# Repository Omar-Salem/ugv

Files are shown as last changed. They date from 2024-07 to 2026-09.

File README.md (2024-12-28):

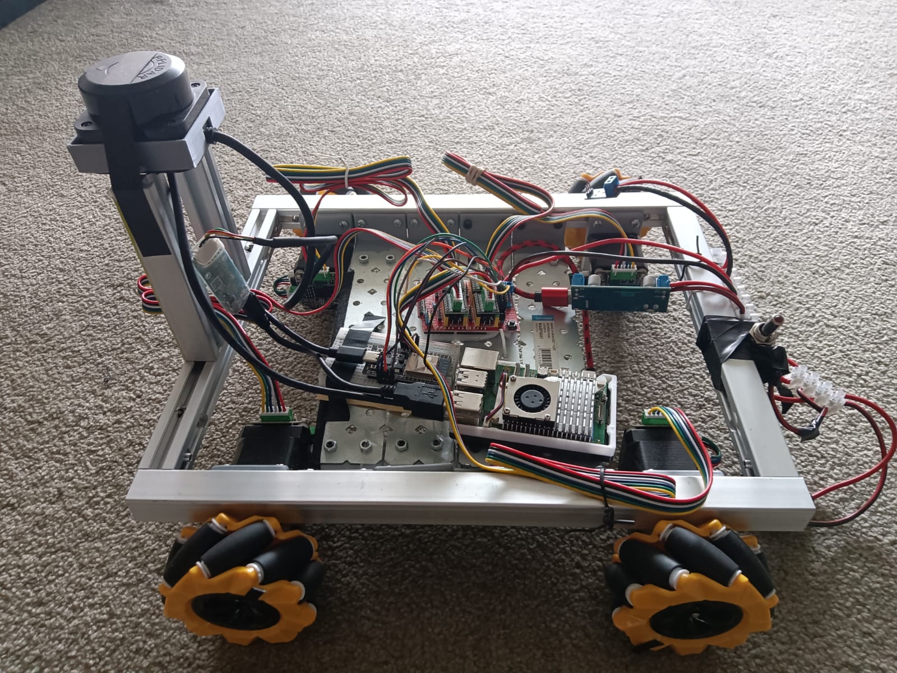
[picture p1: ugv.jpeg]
UGV


# Requirements
## Jazzy
```bash
sudo apt update && sudo apt upgrade

# Set locale
locale  # check for UTF-8

sudo apt install locales
sudo locale-gen en_US en_US.UTF-8
sudo update-locale LC_ALL=en_US.UTF-8 LANG=en_US.UTF-8
export LANG=en_US.UTF-8

locale  # verify settings

# You will need to add the ROS 2 apt repository to your system.
sudo apt install software-properties-common -y
sudo add-apt-repository universe -y

# Now add the ROS 2 GPG key with apt.
sudo apt update && sudo apt install curl -y
sudo curl -sSL https://raw.githubusercontent.com/ros/rosdistro/master/ros.key -o /usr/share/keyrings/ros-archive-keyring.gpg

# Then add the repository to your sources list.
echo "deb [arch=$(dpkg --print-architecture) signed-by=/usr/share/keyrings/ros-archive-keyring.gpg] http://packages.ros.org/ros2/ubuntu $(. /etc/os-release && echo $UBUNTU_CODENAME) main" | sudo tee /etc/apt/sources.list.d/ros2.list > /dev/null

# Install development tools 
sudo apt update && sudo apt install ros-dev-tools

# Install ROS 2
sudo apt update && sudo apt upgrade && sudo apt install ros-jazzy-desktop -y

sudo tee -a ~/.bashrc <<EOL
export ROS_DOMAIN_ID=0
export QT_QPA_PLATFORM=xcb rviz2
export RMW_IMPLEMENTATION=rmw_cyclonedds_cpp
source /opt/ros/jazzy/setup.bash
source ~/microros_ws/install/local_setup.bash
EOL
source ~/.bashrc
sudo apt-get install python3-rosdep -y
echo ${ROS_DISTRO}
````
## Packages
````bash
sudo apt-get install -y ros-${ROS_DISTRO}-slam-toolbox ros-${ROS_DISTRO}-joint-state-publisher ros-${ROS_DISTRO}-robot-state-publisher ros-${ROS_DISTRO}-xacro
sudo apt install -y ros-${ROS_DISTRO}-ros2-control
sudo apt install -y ros-${ROS_DISTRO}-joint-state-publisher-gui
sudo apt install -y ros-${ROS_DISTRO}-ros2-controllers
sudo apt install -y ros-${ROS_DISTRO}-robot-localization
sudo apt install -y ros-${ROS_DISTRO}-navigation2
sudo apt install -y ros-${ROS_DISTRO}-nav2-bringup
sudo apt install -y ros-${ROS_DISTRO}-controller-manager
sudo apt install -y ros-${ROS_DISTRO}-rosbag2
sudo apt install -y ros-${ROS_DISTRO}-behaviortree-cpp-v3
sudo apt install -y ros-${ROS_DISTRO}-tf-transformations
sudo apt-get install -y ros-${ROS_DISTRO}-image-tools
sudo apt-get install -y ros-${ROS_DISTRO}-cartographer

sudo apt install -y ros-${ROS_DISTRO}-angles
sudo apt install -y ros-${ROS_DISTRO}-mqtt-client
sudo apt install -y ros-${ROS_DISTRO}-launch-xml
sudo apt install -y ros-${ROS_DISTRO}-rmw-cyclonedds-cpp ros-${ROS_DISTRO}-tf2-ros ros-${ROS_DISTRO}-tf2-tools
sudo apt install -y python3-colcon-common-extensions
sudo apt-get install -y ros-${ROS_DISTRO}-rviz2 
sudo apt install -y ros-${ROS_DISTRO}-ros-gz
sudo apt install -y ros-${ROS_DISTRO}-gz-ros2-control
sudo apt install vim -y
sudo usermod -aG dialout ${USER}
````

## microros
https://www.hackster.io/514301/micro-ros-on-esp32-using-arduino-ide-1360ca
````bash
cd ~
mkdir microros_ws
cd microros_ws
git clone -b $ROS_DISTRO https://github.com/micro-ROS/micro_ros_setup.git src/micro_ros_setup
sudo apt update && rosdep update
rosdep install --from-paths src --ignore-src -y
sudo apt-get install -y python3-pip
colcon build
source install/local_setup.bash
ros2 run micro_ros_setup create_agent_ws.sh
ros2 run micro_ros_setup build_agent.sh
````

## ROS Control Determinism
````bash
sudo addgroup realtime && sudo usermod -a -G realtime $(whoami)

sudo tee -a /etc/security/limits.conf <<EOL
@realtime soft rtprio 99
@realtime soft priority 99
@realtime soft memlock 102400
@realtime hard rtprio 99
@realtime hard priority 99
@realtime hard memlock 102400
EOL
````

## Git config and SSH key
````bash
git config --global user.email "omar.gamil.salem@gmail.com"
git config --global user.name "Omar Salem"
ssh-keygen -t ed25519 -C "omar.gamil.salem@gmail.com"
cat ~/.ssh/id_ed25519.pub
````

## Create workspace and clone repo
````bash
mkdir -p ~/ugv_ws/src
cd ~/ugv_ws/src 
git clone git@github.com:Omar-Salem/ugv.git .
cd ~/ugv_ws
colcon build 
````

## Shutdown shortcut
````bash
echo "alias off='sudo shutdown -h now'" >> ~/.bash_aliases
````

## Run
### Display

```bash
cd ~/ugv_ws && colcon build --packages-select ugv_description && source install/setup.bash && ros2 launch ugv_description display.launch.py use_gui:=true use_joint_state_publisher:=true
```

### Control
```bash
cd ~/ugv_ws && colcon build --packages-select ugv_control && source install/setup.bash && ros2 launch ugv_control gazebo.launch.py
```

### Mapping
```bash
cd ~/ugv_ws && colcon build --packages-select ugv_mapping && source install/setup.bash && ros2 launch ugv_mapping gazebo.launch.py
```

### Navigation
```bash
cd ~/ugv_ws && colcon build --packages-select ugv_nav && source install/setup.bash && ros2 launch ugv_nav gazebo.launch.py
```

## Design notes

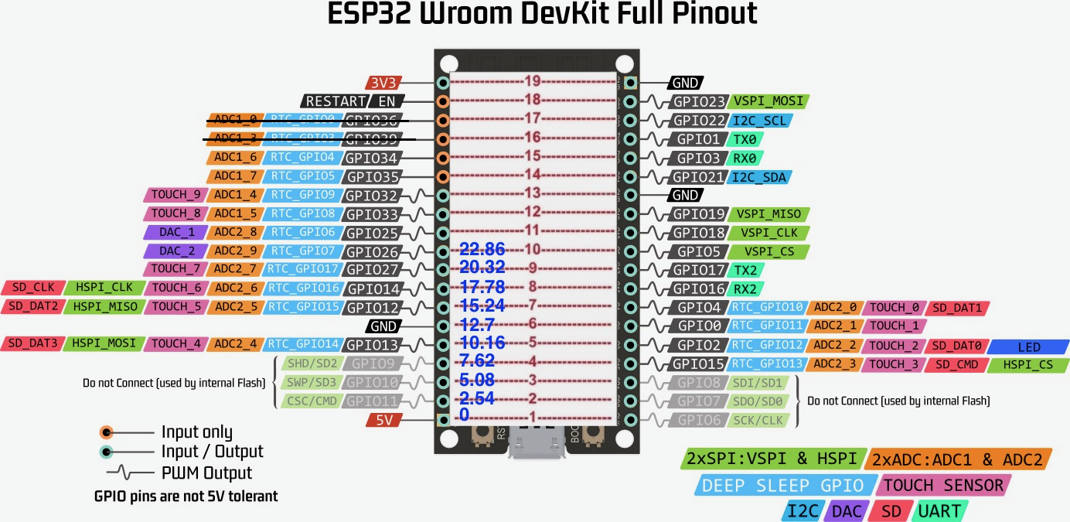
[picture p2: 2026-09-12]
ugv_firmware/docs/esp32 breadboard pinout.png

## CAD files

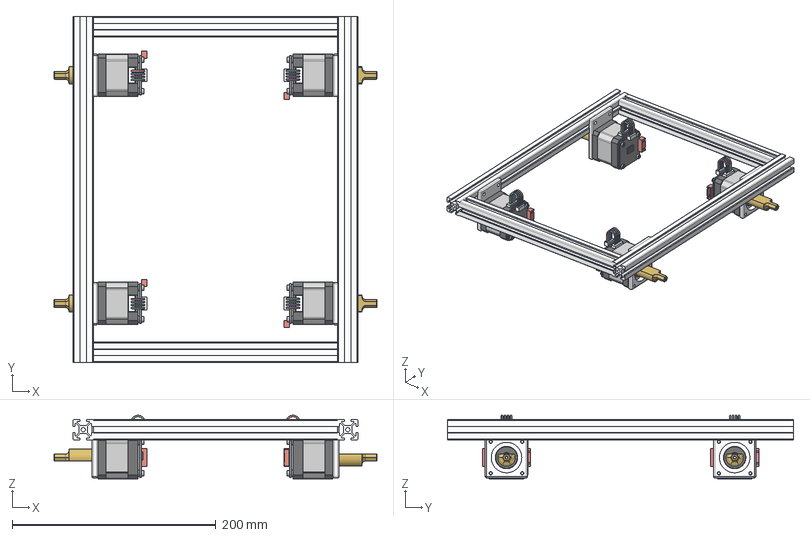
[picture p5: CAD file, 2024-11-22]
base_link_colour.step
317.3 x 340.0 x 62.6 mm
base_link
Motor
Motor (1)
Motor (2)
Motor (2) (1)

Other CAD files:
base_link_colour.f3d
ugv.f3d

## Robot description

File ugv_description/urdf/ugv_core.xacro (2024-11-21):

<?xml version="1.0"?>
<robot name="ugv" xmlns:xacro="http://www.ros.org/wiki/xacro">

    <xacro:include filename="$(find ugv_description)/gazebo/common_inertias.xacro" />

    <xacro:property name="wheel_radius" value="0.0395" />
    <xacro:property name="wheel_thickness" value="0.0369" />
    <xacro:property name="wheel_mass" value="0.05" />

    <xacro:property name="chassis_length" value="0.34" />
    <xacro:property name="chassis_width" value="0.285" />
    <xacro:property name="chassis_height" value="0.02" />
    <xacro:property name="chassis_mass" value="1.0" />
    <xacro:property name="chassis_offset_z" value="${wheel_radius}" />

    <xacro:property name="lidar_radius" value="0.02" />
    <xacro:property name="lidar_thickness" value="0.1" />
    <xacro:property name="lidar_mass" value="0.05" />

    <xacro:property name="edge_thickness" value="0.02" />
    <xacro:property name="edge_to_motor_mount" value="0.016" />
    <xacro:property name="motor_mount_width" value="0.0417" />
    <xacro:property name="motor_shaft_to_edge_x" value="${edge_thickness+edge_to_motor_mount+motor_mount_width/2}" />
    <xacro:property name="wheel_offset_x" value="${chassis_length/2-motor_shaft_to_edge_x}" />

    <xacro:property name="wheels_y_distance_edge_to_edge" value=".36"/>
    <xacro:property name="wheel_offset_y" value="${wheels_y_distance_edge_to_edge/2 - wheel_thickness/2}"/>

    <xacro:property name="wheel_offset_z" value="0.01" />

    <material name="orange">
        <color rgba="1 0.3 0.1 1" />
    </material>

    <material name="yellow">
        <color rgba="1 1 0 1" />
    </material>

    <material name="black">
        <color rgba="0 0 0 1" />
    </material>

    <xacro:macro name="wheel" params="prefix">
        <link name="${prefix}_wheel">
            <visual>
                <origin rpy="${pi/2} 0 0" xyz="0 0 0"/>
                <geometry>
                    <cylinder radius="${wheel_radius}" length="${wheel_thickness}" />
                </geometry>
                <material name="orange" />
            </visual>
            <collision>
                <origin rpy="${pi/2} 0 0" xyz="0 0 0"/>
                <geometry>
                    <cylinder radius="${wheel_radius}" length="${wheel_thickness}" />
                </geometry>
            </collision>
            <xacro:inertial_cylinder mass="${wheel_mass}" length="${wheel_thickness}" radius="${wheel_radius}">
                <origin xyz="0 0 0" rpy="0 0 0" />
            </xacro:inertial_cylinder>
        </link>
    </xacro:macro>

    <link name="base_link">
        <visual>
            <origin rpy="0 0 0" xyz="0 0 ${chassis_offset_z}"/>
            <geometry>
                <box size="${chassis_length} ${chassis_width} ${chassis_height}" />
            </geometry>
            <material name="black" />
        </visual>
        <collision>
            <origin rpy="0 0 0" xyz="0 0 ${chassis_offset_z}"/>
            <geometry>
                <box size="${chassis_length} ${chassis_width} ${chassis_height}" />
            </geometry>
        </collision>
        <xacro:inertial_box mass="${chassis_mass}" x="${chassis_length}" y="${chassis_width}" z="${chassis_height}">
            <origin rpy="0 0 0" xyz="0 0 ${chassis_offset_z}"/>
        </xacro:inertial_box>
    </link>

    <link name="base_footprint" />

    <joint name="base_footprint_joint" type="fixed">
        <parent link="base_link" />
        <child link="base_footprint" />
        <origin xyz="0 0 0" rpy="0 0 0" />
    </joint>

    <xacro:wheel prefix="front_right" />


    <joint name="front_right_wheel_joint" type="continuous">
        <parent link="base_link" />
        <child link="front_right_wheel" />
        <origin xyz="${wheel_offset_x} ${-wheel_offset_y} ${wheel_radius}" />
        <axis xyz="0.0 1.0 0.0" />
    </joint>


    <xacro:wheel prefix="front_left" />

    <joint name="front_left_wheel_joint" type="continuous">
        <parent link="base_link" />
        <child link="front_left_wheel" />
        <origin xyz="${wheel_offset_x} ${wheel_offset_y} ${wheel_radius}" />
        <axis xyz="0.0 1.0 0.0" />
    </joint>

    <xacro:wheel prefix="rear_right" />

    <joint name="rear_right_wheel_joint" type="continuous">
        <parent link="base_link" />
        <child link="rear_right_wheel" />
        <origin xyz="${-wheel_offset_x} ${-wheel_offset_y} ${wheel_radius}" />
        <axis xyz="-0.0 1.0 0.0" />
    </joint>

    <xacro:wheel prefix="rear_left" />

    <joint name="rear_left_wheel_joint" type="continuous">
        <parent link="base_link" />
        <child link="rear_left_wheel" />
        <origin xyz="${-wheel_offset_x} ${wheel_offset_y} ${wheel_radius}" />
        <axis xyz="0.0 1.0 0.0" />
    </joint>

    <link name="lidar_link">
        <visual>
            <origin xyz="0 0 0" rpy="0 0 0"/>
            <geometry>
                <cylinder radius="${lidar_radius}" length="${lidar_thickness}" />     </geometry>
            <material name="yellow"/>
        </visual>
        <collision>
            <origin xyz="0 0 0" rpy="0 0 0"/>
            <geometry>
                <cylinder radius="${lidar_radius}" length="${lidar_thickness}" />    
            </geometry>
        </collision>
        <xacro:inertial_cylinder mass="${lidar_mass}" length="${lidar_thickness}" radius="${lidar_radius}">
            <origin xyz="0 0 0" rpy="0 0 0" />
        </xacro:inertial_cylinder>
    </link>

    <joint name="lidar_link_joint" type="fixed">
        <parent link="base_link"/>
        <child link="lidar_link"/>
        <origin xyz="${chassis_length/2-lidar_radius} 0 ${chassis_offset_z+lidar_thickness/2}" rpy="0 0 ${pi}"/>
    </joint> 

</robot>

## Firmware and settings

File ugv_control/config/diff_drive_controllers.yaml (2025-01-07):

controller_manager:
  ros__parameters:
    update_rate: 10  # Hz

    joint_state_broadcaster:
      type: joint_state_broadcaster/JointStateBroadcaster

    diff_drive_controller:
      type: diff_drive_controller/DiffDriveController

diff_drive_controller:
  ros__parameters:
    type: diff_drive_controller/DiffDriveController
    wheels_per_side: 2
    left_wheel_names: [ "rear_left_wheel_joint" ,"front_left_wheel_joint" ]
    right_wheel_names: [ "rear_right_wheel_joint", "front_right_wheel_joint" ]

    wheel_separation: 0.34
    wheel_separation_multiplier: 1.6 #TODO revise
    wheel_radius: 0.0395
    
    position_feedback: true
    open_loop: false
    cmd_vel_timeout: 0.1
    base_frame_id: base_link

    linear.x.has_velocity_limits: true
    linear.x.max_velocity: 0.2
    linear.x.min_velocity: -0.2

    angular.z.has_velocity_limits: true
    angular.z.max_velocity: 0.3
    angular.z.min_velocity: -0.3

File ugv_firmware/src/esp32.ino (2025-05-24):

// https://www.hackster.io/514301/micro-ros-on-esp32-using-arduino-ide-1360ca
// https://github.com/micro-ROS/micro_ros_platformio

#include <Arduino.h>
#include <Motor.h>
#include <micro_ros_platformio.h>
#include <rcl/rcl.h>
#include <rclc/rclc.h>
#include <rclc/executor.h>

#include <ugv_interfaces/msg/motors_odom.h>

#if !defined(MICRO_ROS_TRANSPORT_ARDUINO_SERIAL)
#error This example is only avaliable for Arduino framework with serial transport.
#endif

rcl_subscription_t velocityCommandSubscriber;
ugv_interfaces__msg__MotorsOdom velocityCommandCallbackMessage;
rclc_executor_t subscriberExecutor;

rcl_publisher_t odomStatePublisher;
rclc_executor_t publisherExecutor;

rclc_support_t support;
rcl_allocator_t allocator;
rcl_node_t node;
rcl_timer_t publisherTimer;
const unsigned int PUBLISHER_TIMER_TIMEOUT_MILL = 100;

// X
const int REAR_LEFT_STEP = 26; //Brown
const int REAR_LEFT_DIR = 16; //Violet
Motor rearLeftWheel(REAR_LEFT_STEP, REAR_LEFT_DIR);

// Y
const int FRONT_LEFT_STEP = 27; //Green
const int FRONT_LEFT_DIR = 17; //Blue
Motor frontLeftWheel(FRONT_LEFT_STEP, FRONT_LEFT_DIR);

// Z
const int REAR_RIGHT_STEP = 14; //White
const int REAR_RIGHT_DIR = 18; //Orange
Motor rearRightWheel(REAR_RIGHT_STEP, REAR_RIGHT_DIR);

// A
const int FRONT_RIGHT_STEP = 25; //Yellow
const int FRONT_RIGHT_DIR = 4; //Grey
Motor frontRightWheel(FRONT_RIGHT_STEP, FRONT_RIGHT_DIR);

//GND Black

/**

 *   C  N  C
 * Violet   Blue    Orange    Grey     Black
 * Brown    Green   White     Yellow   
 */

Motor *motors[4] = {&rearLeftWheel,
                    &rearRightWheel,
                    &frontLeftWheel,
                    &frontRightWheel};

// https://randomnerdtutorials.com/esp32-dual-core-arduino-ide/
TaskHandle_t moveMotorsTask;

// #define RCCHECK(fn) { rcl_ret_t temp_rc = fn; if((temp_rc != RCL_RET_OK)){error_loop();}}
#define RCSOFTCHECK(fn)                \
    {                                  \
        rcl_ret_t temp_rc = fn;        \
        if ((temp_rc != RCL_RET_OK))   \
        {                              \
            printf("NOOOOOOOOOOOOOO"); \
        }                              \
    }

void velocityCommandCallback(const void *msgin)
{
    const ugv_interfaces__msg__MotorsOdom *command = (const ugv_interfaces__msg__MotorsOdom *)msgin;
    rearLeftWheel.setSpeed(command->rear_left);
    frontLeftWheel.setSpeed(command->front_left);

    rearRightWheel.setSpeed(command->rear_right);
    frontRightWheel.setSpeed(command->front_right);
}

void odomStateTimerCallback(rcl_timer_t *timer, int64_t last_call_time)
{
    RCLC_UNUSED(last_call_time);
    if (timer != NULL)
    {
        ugv_interfaces__msg__MotorsOdom msg;

        msg.rear_left = rearLeftWheel.getCurrentPosition();
        msg.rear_right = rearRightWheel.getCurrentPosition();

        msg.front_left = frontLeftWheel.getCurrentPosition();
        msg.front_right = frontRightWheel.getCurrentPosition();

        RCSOFTCHECK(rcl_publish(&odomStatePublisher, &msg, NULL));
    }
}

void createStatePublisher()
{

    const rosidl_message_type_support_t *type_support = ROSIDL_GET_MSG_TYPE_SUPPORT(ugv_interfaces, msg,
                                                                                    MotorsOdom);

    RCSOFTCHECK(rclc_publisher_init_default(
        &odomStatePublisher,
        &node,
        type_support,
        "ugv/motors_state"));

    // create timer
    RCSOFTCHECK(rclc_timer_init_default(
        &publisherTimer,
        &support,
        RCL_MS_TO_NS(PUBLISHER_TIMER_TIMEOUT_MILL),
        odomStateTimerCallback));

    // create executor
    RCSOFTCHECK(rclc_executor_init(&publisherExecutor, &support.context, 1, &allocator));
    RCSOFTCHECK(rclc_executor_add_timer(&publisherExecutor, &publisherTimer));
}

void createCommandSubscriber()
{
    const rosidl_message_type_support_t *type_support = ROSIDL_GET_MSG_TYPE_SUPPORT(ugv_interfaces, msg,
                                                                                    MotorsOdom);

    RCSOFTCHECK(rclc_subscription_init_default(
        &velocityCommandSubscriber,
        &node,
        type_support,
        "ugv/motors_cmd"));

    RCSOFTCHECK(rclc_executor_init(&subscriberExecutor, &support.context, 1, &allocator));

    RCSOFTCHECK(rclc_executor_add_subscription(&subscriberExecutor,
                                               &velocityCommandSubscriber,
                                               &velocityCommandCallbackMessage,
                                               &velocityCommandCallback,
                                               ON_NEW_DATA));
}

void setup()
{
    Serial.begin(115200);
    set_microros_serial_transports(Serial);

    allocator = rcl_get_default_allocator();

    RCSOFTCHECK(rclc_support_init(&support, 0, NULL, &allocator));

    RCSOFTCHECK(rclc_node_init_default(&node, "micro_ros_ugv_motors", "", &support));

    createStatePublisher();

    createCommandSubscriber();

    xTaskCreatePinnedToCore(
        moveMotors,       /* Task function. */
        "moveMotorsTask", /* name of task. */
        10000,            /* Stack size of task */
        NULL,             /* parameter of the task */
        0,                /* priority of the task */
        &moveMotorsTask,  /* Task handle to keep track of created task */
        0);               /* pin task to core 1 */
}

void loop()
{
    RCSOFTCHECK(rclc_executor_spin_some(&publisherExecutor, RCL_MS_TO_NS(50)));
    RCSOFTCHECK(rclc_executor_spin_some(&subscriberExecutor, RCL_MS_TO_NS(50)));
}

void moveMotors(void *pvParameters)
{
    for (;;)
    {
        for (auto s : motors)
        {
            s->run();
        }
    }
}

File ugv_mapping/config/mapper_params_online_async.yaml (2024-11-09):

slam_toolbox:
  ros__parameters:

    # Plugin params
    solver_plugin: solver_plugins::CeresSolver
    ceres_linear_solver: SPARSE_NORMAL_CHOLESKY
    ceres_preconditioner: SCHUR_JACOBI
    ceres_trust_strategy: LEVENBERG_MARQUARDT
    ceres_dogleg_type: TRADITIONAL_DOGLEG
    ceres_loss_function: None

    # ROS Parameters
    odom_frame: odom
    map_frame: map
    base_frame: base_footprint
    scan_topic: /scan
    use_map_saver: true
    mode: mapping #TODO pass in runtime
    # mode: localization 
    
    # if you'd like to immediately start continuing a map at a given pose
    # or at the dock, but they are mutually exclusive, if pose is given
    # will use pose
    map_file_name: /home/omar.salem/ugv_ws/src/ugv_mapping/maps/apartment/map
    map_start_pose: [0.0, 0.0, 0.0]
    # map_start_at_dock: true

    debug_logging: false
    throttle_scans: 1
    transform_publish_period: 0.02 #if 0 never publishes odometry
    map_update_interval: 5.0
    resolution: 0.05
    max_laser_range: 16.0 
    minimum_time_interval: 0.5
    transform_timeout: 0.2
    tf_buffer_duration: 30.
    stack_size_to_use: 40000000 #// program needs a larger stack size to serialize large maps
    enable_interactive_mode: true

    # General Parameters
    use_scan_matching: true
    use_scan_barycenter: true
    minimum_travel_distance: 0.5
    minimum_travel_heading: 0.5
    scan_buffer_size: 10
    scan_buffer_maximum_scan_distance: 10.0
    link_match_minimum_response_fine: 0.1
    link_scan_maximum_distance: 1.5
    loop_search_maximum_distance: 3.0
    do_loop_closing: true
    loop_match_minimum_chain_size: 10
    loop_match_maximum_variance_coarse: 3.0
    loop_match_minimum_response_coarse: 0.35
    loop_match_minimum_response_fine: 0.45

    # Correlation Parameters - Correlation Parameters
    correlation_search_space_dimension: 0.5
    correlation_search_space_resolution: 0.01
    correlation_search_space_smear_deviation: 0.1

    # Correlation Parameters - Loop Closure Parameters
    loop_search_space_dimension: 8.0
    loop_search_space_resolution: 0.05
    loop_search_space_smear_deviation: 0.03

    # Scan Matcher Parameters
    distance_variance_penalty: 0.5
    angle_variance_penalty: 1.0

    fine_search_angle_offset: 0.00349
    coarse_search_angle_offset: 0.349
    coarse_angle_resolution: 0.0349
    minimum_angle_penalty: 0.9
    minimum_distance_penalty: 0.5
    use_response_expansion: true

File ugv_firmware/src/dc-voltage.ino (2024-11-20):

// /*
//   Arduino DC Voltage Demo 1
//   dc-voltage-demo.ino
//   Use Arduino A/D converter to measure voltage
//   Use external voltage divider with 30k & 7.5k resistors
//   Results displayed on Serial Monitor

//   DroneBot Workshop 2021
//   https://dronebotworkshop.com
// */
// #include <Wire.h>
// #include <Adafruit_SSD1306.h>
// #include <Adafruit_GFX.h>

// // Define analog input
// #define ANALOG_IN_PIN 13

// #define OLED_WIDTH 128
// #define OLED_HEIGHT 64
// #define OLED_ADDR   0x3C

// // Floats for ADC voltage & Input voltage
// float adc_voltage = 0.0;
// float in_voltage = 0.0;

// // Floats for resistor values in divider (in ohms)
// float R1 = 30000.0;
// float R2 = 7500.0; 

// // Float for Reference Voltage
// float ref_voltage = .89;

// // Integer for ADC value
// int adc_value = 0;

// Adafruit_SSD1306 display(OLED_WIDTH, OLED_HEIGHT);
// void setup(){

//   display.begin(SSD1306_SWITCHCAPVCC, OLED_ADDR);
// }

// void loop(){
//    // Read the Analog Input
//    adc_value = analogRead(ANALOG_IN_PIN);
   
//    // Determine voltage at ADC input
//    adc_voltage  = (adc_value * ref_voltage) / 1024.0; 
   
//    // Calculate voltage at divider input
//    in_voltage = adc_voltage / (R2/(R1+R2)); 
   
//   display.clearDisplay();

//   display.setTextSize(1);
//   display.setTextColor(WHITE);
//   display.setCursor(0, 0);
//   display.print("Voltage:");
//   display.println(in_voltage);

//   display.display();
  
//   // Short delay
//   delay(500);
// }

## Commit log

2024-04-29 -passed args to ugv.xacro -added control, gazebo folders to share directory
    [gazebo.xacro, gazebo_control.xacro, joints.macro.xacro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]
2024-04-29 -fixed joints path in gazebo
    [gazebo_control.xacro]
2024-04-30 -removed _1 postfix from wheels' names -using bool in launch files
    [diff_drive_controllers.yaml, front_left_wheel.stl, front_right_wheel.stl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]
2024-04-30 -made wheel_radius double
    [diff_drive_controllers.yaml]
2024-04-30 -updated wheel_separation and update_rate
    [diff_drive_controllers.yaml]
2024-04-30 -removed limits and velocity state from joints
    [joints.macro.xacro]
2024-04-30 -common macro file
    [gazebo.xacro, lidar.xacro, ugv.macro.xacro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]
2024-04-30 -gazebo wheel colours
    [gazebo.xacro]
2024-04-30 -ugv_chassis_firmware package
    [ros2_control.xacro]
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2024-05-03 -updated masses
    [ugv_core.xacro]
2024-05-03 -fixed mirrored axis!
    [ugv_core.xacro]
2024-05-03 -new design
    [base_link.stl, front_left_wheel.stl, front_right_wheel.stl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]
2024-05-03 -f3d file
    [ugv v14.f3d]
2024-05-06 added map and laserscan to display.rviz
2024-05-06 inertia macros
    [ugv_core.xacro]
2024-05-07 -passing gazebo world to control launch
    [ugv_core.xacro]
2024-05-25 -reverted esp32.ino
2024-06-18 working! publishing to correct topic
    [esp32.ino]
2024-06-18 setting reverse direction for left side
    [basic.ino, esp32.ino]
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2024-06-19 disabled front_left_wheel_joint and front_right_wheel_joint
    [joints.macro.xacro]
2024-06-22 fixed motors!! disabled microstepping
    [basic.ino]
2024-06-28 fixed urdf + inertia
    [base_link.stl, common_inertias.xacro, diff_drive_controllers.yaml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]
2024-06-28 urdf lidar
    [ugv_core.xacro]
2024-06-28 lidar urdf
    [ugv_core.xacro]
2024-06-28 fixed inertia
    [ugv_core.xacro]
2024-07-05 Updated wheel_offset_x and wheel_offset_y
    [ugv_core.xacro]
2024-07-11 updated board_microros_distro to jazzy
2024-07-11 checking all 4 motors topic
2024-07-11 setting max speed to 500 steps per second + inverting right wheels
    [esp32.ino]
2024-07-11 using array of steppers
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2024-07-13 added power supply to wiring diagram
    [Wiring.fzz]
2024-07-13 Organized wiring
    [Wiring.fzz]
2024-07-13 organize PCB
    [Wiring.fzz]
2024-07-13 better wiring
    [Wiring.fzz]
2024-07-14 one layer PCB
    [PCB.fzz]
2024-07-14 double sided PCB
    [PCB.fzz]
2024-07-20 changed pins, removed 5v connection
    [PCB.fzz, Wiring.fzz]
2024-07-20 using array of pointers
    [PCB.fzz]
2024-07-20 upper case of const variables
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2024-07-20 -switched from cmd_vel_unstamped to cmd_vel -added missing motors to command and state interfaces -README
    [ugv_chassis_hardware.cpp]
2024-07-20 using a vector to hold motor instances
2024-07-20 -cleared dead code from diff drive controller config -lowered speed in test command to 1 cm p/s
    [diff_drive_controllers.yaml]
2024-07-20 increased cmd_vel_timeout to 1 second
    [diff_drive_controllers.yaml]
2024-07-23 converted wheels from unique_ptr to shared_ptr
2024-07-24 migrate to gazebo harmonic
    [gazebo.xacro, lidar.xacro, ugv.macro.xacro]
2024-07-26 updated wheel_radius to 0.0375 m
    [diff_drive_controllers.yaml]
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2024-07-29 passing urdf to display
2024-08-01 removed 5v & GND connection
    [PCB.fzz]
2024-08-16 ugv_description c++ package
    [ugv v3.f3d]
2024-08-20 lidar working!
    [lidar.xacro]
2024-08-21 gazebo launch file
    [empty_world.sdf]
2024-08-21 fixed lidar
    [lidar.xacro]
2024-08-21 gazebo control plugin
    [gazebo_control.xacro]
2024-08-22 removed empty tag
    [gazebo_control.xacro]
2024-08-31 gazebo working!
    [diff_drive_controllers.yaml]
2024-09-01 made base_footprint parent
    [diff_drive_controllers.yaml, ugv_core.xacro]
2024-09-03 switched base_link nd base_footprint
    [diff_drive_controllers.yaml, ugv_core.xacro]
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2024-09-13 added diff_drive_controller type in yaml
    [diff_drive_controllers.yaml]
2024-09-13 added diff_drive_controller type + disabling rviz by default
    [diff_drive_controllers.yaml]
2024-09-18 minimized PCB size + connected ground
    [PCB.fzz]
2024-09-18 compressed PCB. single layer
    [PCB.fzz]
2024-09-18 text placement
    [PCB.fzz]
2024-09-18 compressed PCB
    [PCB.fzz]
2024-09-18 reverted to double layer PCB
    [PCB.fzz]
2024-09-18 .double layer
    [PCB.fzz]
2024-09-18 fixed getting motors position
    [Motor.cpp]
2024-09-19 updated wheel_separation and cmd_vel_timeout
    [diff_drive_controllers.yaml]
2024-09-20 fixing lidar run issue
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2024-09-22 switched usb ports for microros and lidar + passed correct frame_id to lidar
2024-09-27 fixed wheel_separation and max_laser_range
    [diff_drive_controllers.yaml]
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2024-09-27 updated wheel_radius
    [diff_drive_controllers.yaml]
2024-09-28 fixed wheel_separation
    [diff_drive_controllers.yaml]
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2024-11-03 increased nav min velocity set mapping mode to mapping
2024-11-03 min and max linear & angular velocity
    [diff_drive_controllers.yaml]
2024-11-03 fixed lidar rotation!!
    [ugv_core.xacro]
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2024-11-04 increased linear & angular velocity limits + Keeping just 1 message in rviz Odom + added maps
    [diff_drive_controllers.yaml]
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2024-11-07 walls world
    [walls.sdf]
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2024-11-08 updated gazebo lidar max rang to 16.0
    [lidar.xacro]
2024-11-20 increased controller_server frequency and removed velocity and acceleration limits
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2024-11-21 updated wheel_radius in xacro
    [ugv_core.xacro]
2024-11-21 added wheel_separation_multiplier TODO
    [diff_drive_controllers.yaml]
2024-11-22 Added Chassis.step
    [Chassis.step]
2024-11-22 Update Chassis.step, base_link.f3d, and base_link_colour.f3d
    [Chassis.step, base_link.f3d, base_link_colour.f3d]
2024-11-22 Update base_link.f3d and base_link_colour.step
    [base_link.f3d, base_link_colour.step]
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2024-11-24 Update base_link.f3d and ugv.f3d
    [base_link.f3d, ugv.f3d]
2024-11-24 Update base_link_colour.step and ugv.f3d
    [ugv.f3d]
2024-11-24 cleanup xacro
    [ugv.macro.xacro, ugv.urdf]
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2024-12-28 fixed gazebo odometry by using gz-sim-diff-drive-system
    [gazebo_control.xacro]
2025-01-07 updated wheel_separation and update_rate
    [diff_drive_controllers.yaml]
2025-01-07 added publish rate to sanity check velocity command
2025-01-07 split hw interface and firmware
    [PCB.fzz, ros2_control.xacro]
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
